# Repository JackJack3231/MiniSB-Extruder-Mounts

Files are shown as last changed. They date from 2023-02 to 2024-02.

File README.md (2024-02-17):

# MiniSB-Extruder-Mounts

Remix of the Mini-Stealthburner to run other Extruders.

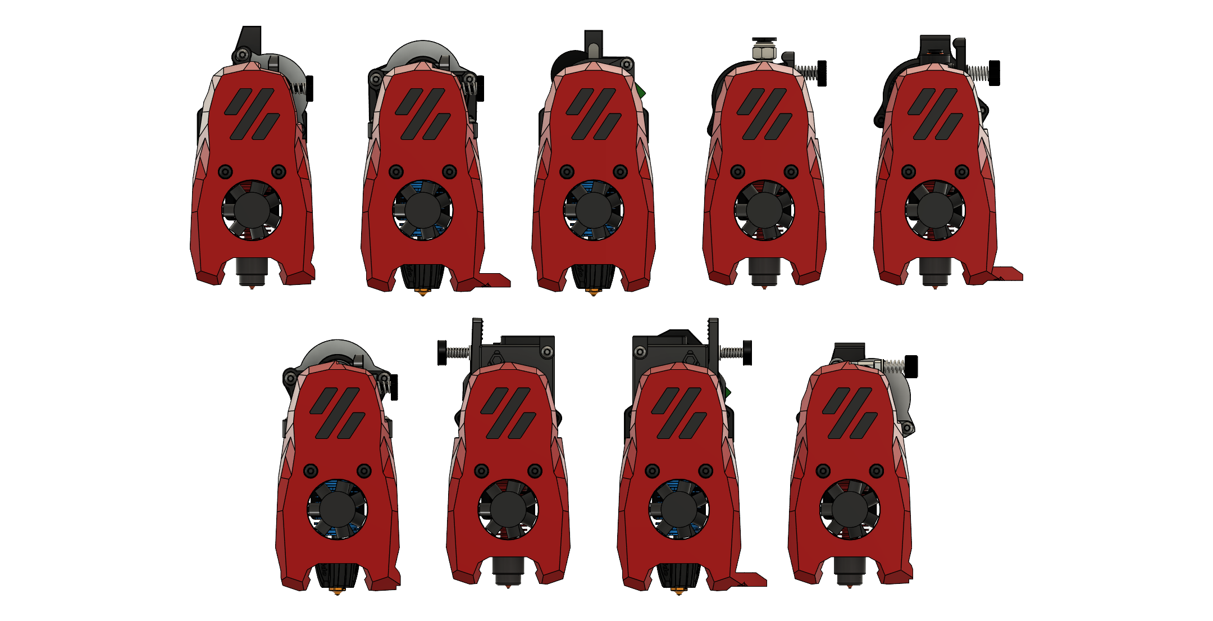
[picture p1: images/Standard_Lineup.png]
Lineup of Standard Extruder-Mounts

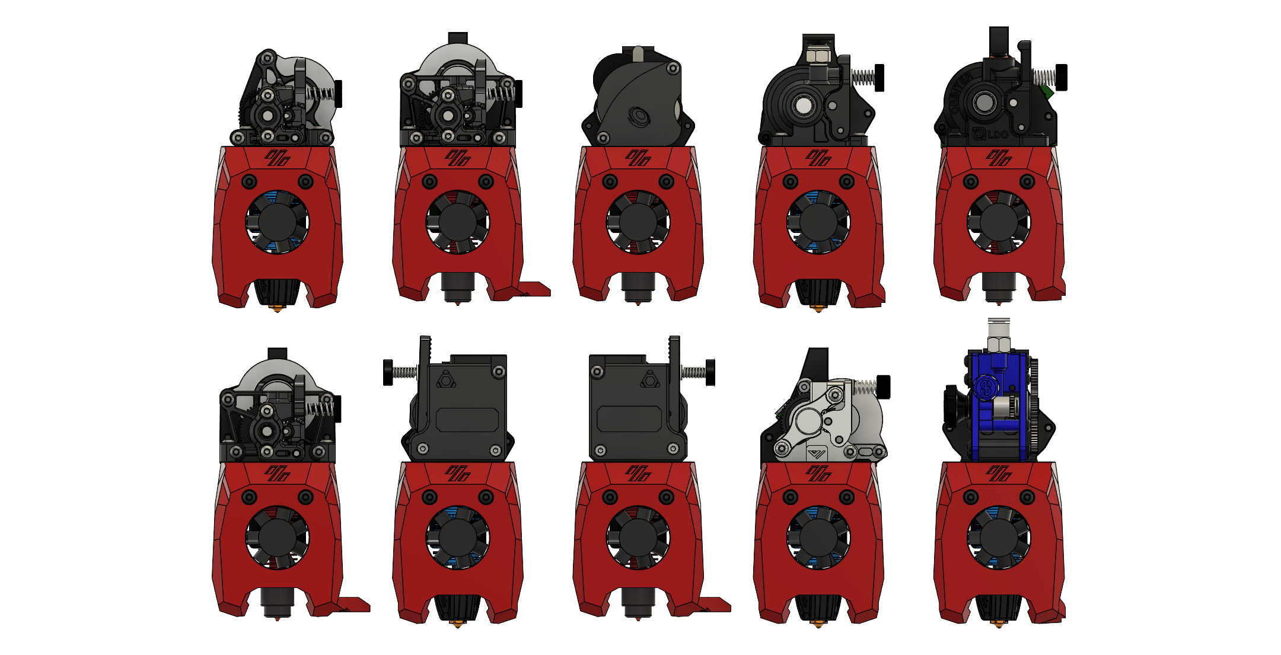
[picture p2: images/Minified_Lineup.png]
Lineup of Minified Extruder-Mounts


This repo includes reworked Files of the Mini-Stealthburner to allow you to use different extruders, namely:

- [Phaetus Apus](https://www.phaetus.com/apus/)
- [Lerdge Aquarius](https://shop.lerdge.com/products/direct-drive-extruder)
- [Haldis HGT](https://www.aliexpress.com/item/1005004816041384.html)
- [Haldis HGX 2.0](https://www.aliexpress.com/item/1005005911670091.html)
- [Haldis HGX-Lite](https://www.aliexpress.com/item/1005004699216563.html)
- [Bondtech LGX-Lite](https://www.bondtech.se/product/lgx-lite-large-gears-extruder/)
- [Mellow Libra Mini](https://www.aliexpress.com/item/1005003506182112.html)
- [Orbiter v1.5](https://orbiterprojects.com/orbiter-1-5/)
- [LDO Orbiter v2.0](https://orbiterprojects.com/orbiter-v2-0/)
- [Annex Engineering Sherpa Heavy](https://github.com/Annex-Engineering/Sherpa_Heavy-Extruder)
- [Annex Engineering Sherpa Micro](https://github.com/Annex-Engineering/Sherpa_Micro-Extruder)
- [Annex Engineering Sherpa Mini](https://github.com/Annex-Engineering/Sherpa_Mini-Extruder)
- TriangleLab TBG-Lite ([Left](https://www.aliexpress.com/item/1005004186141062.html)- and [Right](https://www.aliexpress.com/item/1005003908281100.html)-Version)
- [TriangleLab TBG-S](https://www.aliexpress.com/item/1005005060887127.html)
- [Vz-Hextrudort Low CNC & Vz-Hextrudort Plus CNC](https://github.com/VzBoT3D/Vz-HextrudORT)

The only parts that have changed are the Cowling, Strain-Relief and the Spacers. Everything else is Stock(Hotend Mount, X-Carriage) so this is a drop-in-replacement for Printers with the V0.2-Style X-Carriage.

As I don't have all the extruders some are untested, however if the CAD-Files are accurate they should work fine. This table shows the versions I have verified to work (checkmark):
| Extruder | | Notes |
| --- | --- | ----- |
| Phaetus Apus | :heavy_division_sign: | Assembly works, but needs testing inside a printer |
| Lerdge Aquarius | :heavy_division_sign: | Assembly works, but needs testing inside a printer |
| HGT | :heavy_check_mark: |
| HGX 2.0 | :heavy_check_mark: |
| HGX-Lite | :heavy_division_sign: | Assembly works, but needs testing inside a printer |
| LGX-Lite | :heavy_check_mark: |
| Libra Mini | :grey_question: |
| Orbiter v1.5 | :heavy_division_sign: | Assembly works, but needs testing inside a printer |
| Orbiter v2.0 | :heavy_check_mark: |
| Sherpa Heavy | :grey_question: |
| Sherpa Micro | :heavy_check_mark: |
| Sherpa Mini | :heavy_check_mark: |
| TBG-Lite Left | :heavy_check_mark: |
| TBG-Lite Right | :heavy_check_mark: |
| TBG-S | :heavy_check_mark: |
| Vz-Hextrudort Low CNC | :heavy_check_mark: |
| Vz-Hextrudort Low Plus CNC | :heavy_check_mark: |

## Versions

There are two visual Versions, a "Standard" and a "Minified" Version. The Standard-Version has the upper Logo-Part of the Mini-Stealthburner in front of the Extruder (like [Mavericks LGX-Lite Mod](https://mods.vorondesign.com/detail/nJmiEHmmiI9woW4PqjQ2dA)). The Minified Version doesn't have this cover and is more in line with the Bowden Toolhead or [Mini-AfterSherpa](https://github.com/PrintersForAnts/Mini-AfterSherpa).

### Rapido HF, Dragon UHF and TriangleLab Dragon Ace

Additionally, there are longer cowlings and Hotend mounts to allow you to use a Rapido HF or a Dragon UHF. These versions can be found in the "High_Flow"-Folders of each extruder. **Remember that this will reduce a bit of the usable z height, so update your firmware configuration.**

Also, there is a mount for the [Dragon Ace Hotend](https://www.trianglelab.net/products/dragon-ace%E2%84%A2-hotend) (the mount is exactly the same as the Dragon UHF). With this mount you can use the Dragon Ace with the "Standard Flow" cowlings as it is 3 mm shorter than the Rapido HF or Dragon UHF. Alternatively you can use the spacer that is included with the Dragon ace and use it with the "High Flow" cowlings.

### One Fits Most Version a.k.a. Swiss Cheese

There is a [Version](/Extruder_Mounts/_OneFitsMost/) that aims to support as many extruders as possible, while needing as few printed parts as possible. Dubbed Swiss cheese.

## Bed-Probes

### Boop

The non no probe and ZeroClick cowlings have a cutout for [Boop](https://github.com/PrintersForAnts/Boop).
This is currently untested. The current strain-reliefs and PCB-plates are incompatible,
I recommend using [KayosMakers CANboard Mounts](https://github.com/KayosMaker/CANboard_Mounts).

### Klicky and KlickyNG

For Klicky Users there are cowlings with the probe carrier part for both ["normal" Klicky and KlickyNG](https://github.com/jlas1/Klicky-Probe). The BOM is the same as for a standard Mini-Stealthburner, so for required parts check the [Klicky-Probe GitHub](https://github.com/jlas1/Klicky-Probe).

The Klicky Cowlings have only been test fitted in a V0.2 to check for collisions.
They were not actually used for probing and printing.
As such no docks have been verified to work.

### ZeroClick

Support for the [ZeroClick Probe by zruncho3d](https://github.com/zruncho3d/ZeroClick) is available.

To make space and reduce the chance of collisions, the Dock and Mount have been remade, and special Cowlings are necessary. Also, unlike other remixes of the MiniSB for ZeroClick, this implementation should (barely) allow the use of both Sequin LEDs. More information can be found in the [ZeroClick Common Folder](/Extruder_Mounts/_ZeroClick-Common/).

[Video of ZeroClick in action](https://github.com/JackJack3231/MiniSB-Extruder-Mounts/issues/4#issuecomment-1911860910)

### SuperPINDA, PINDA, M8 inductive probes

SuperPINDA, PINDA and other 8 mm inductive probes are supported. These will require an additional M3x6 BHCS to clamp the probe to the cowling. Clearances are quite tight and there is a very thin wall between the part cooling fan and the probe.

## Strain-Relief and Spacers

Also included are Strain-Reliefs (quickly and crappily thrown together), Mounting Plates for the [Umbilical-PCB by Timmit](https://github.com/VoronDesign/Voron-Hardware/tree/master/V0-Umbilical) and mounting plates for CAN Toolhead boards based on [@KayosMaker/CANboard_Mounts](https://github.com/KayosMaker/CANboard_Mounts). The Umbilical Plates also support the LDO Picobilical. **If you use a PCB Toolhead board please double-check, that the screws on the mounting plate don't short anything!**

The needed Spacers (Size according to CAD) are also included, both in the standard round shape and an octagon version inspired by [KayosMaker](https://github.com/KayosMaker/CANboard_Mounts). The Octagon Spacers are the preferred version, because these don't rely on layer-adhesion for their strength and can be printed lying down instead. Also note that depending on which motor you have on your extruder the Spacer-Length can change because Moons-Motors have a thicker Mounting-Flange (2.5 mm) compared to LDO (2 mm). Keep in mind, when installing the Heatsets into the spacers they can get squished, so the alignment is not 100% correct anymore. If you have issues with this try using longer spacers.

## Print-Instructions

Standard Voron Print-Settings (0.2 mm Layer Height, 4 Perimeters, 40% Infill, 5 Top- and Bottom-Layers). No Supports are needed and all STLs are oriented the correct way and ready to import and print.

## Assembly

Pretty much all the mounts get assembled the same way, important differences get called out in the mount-specific Assembly Manual:

1. Install Heatset-Inserts into Spacers, if your Extruder gets screwed down from the top also install Heatsets into the Cowling
2. Install Fans according to [V0.2 Assembly Manual](https://github.com/VoronDesign/Voron-0/blob/Voron0.2/Manuals/VORON_V0.2_Assembly_Manual.pdf) (page 165-167)
3. Insert the M3 Hex-Nut into the slot on the top of the cowling
4. Secure Extruder to the Cowling with hardware mentioned in the mount-specific BOM
5. Install Hotend, make sure to cut the PTFE-Tube to the correct length.
6. Install everything to the X-Carriage, secure with 2 M3x35 BHCS from the front and 1 M3x20 BHCS from the rear
7. Add Spacers for strain-relief/umbilical plate, you may need to replace some screws to have enough thread to engage with the spacers
8. Add strain-relief/umbilical plate, secure to spacers and X-Carriage

## Credits

The cowling files have been remixed from [Mavericks LGX-Lite Mod](https://mods.vorondesign.com/detail/nJmiEHmmiI9woW4PqjQ2dA).

The Voron [V0.2 files](https://github.com/VoronDesign/Voron-0) have also been used as a reference and are partially included in the CAD-Files uploaded in this repository.

For the umbilical plates [Timmit's PCB CAD](https://github.com/VoronDesign/Voron-Hardware/tree/master/V0-Umbilical) was used.

The CAN-board mounts are remixed from [KayosMakers CANboard Mounts](https://github.com/KayosMaker/CANboard_Mounts)

The Klicky Parts were directly taken from [JosAr's CAD-Files](https://github.com/jlas1/Klicky-Probe) on the Klicky-Probe GitHub.

ZeroClick Parts are based on [zruncho3d's original mod](https://github.com/zruncho3d/ZeroClick).

The CAD-File for the PINDA-Probe was made by Matěj Pavel [Source: GrabCAD](https://grabcad.com/library/prusa-induction-autolevelling-probe-pinda-mk1-1).

Phaetus Hotend CAD-Files come from the [Phaetus GitHub repositories](https://github.com/Phaetus?tab=repositories).

TriangleLab Dragon Ace CAD are from [TriangleLab's Google Drive](https://drive.google.com/drive/folders/11QHxG745J42ZzM7vk0ET1ysG6nBwzrUO).

Sources for the Extruder CAD-Files can be found in the respective README.

## Extras

There are Toolhead Pictures for the Mainsail sidebar included in the Extras Folder.

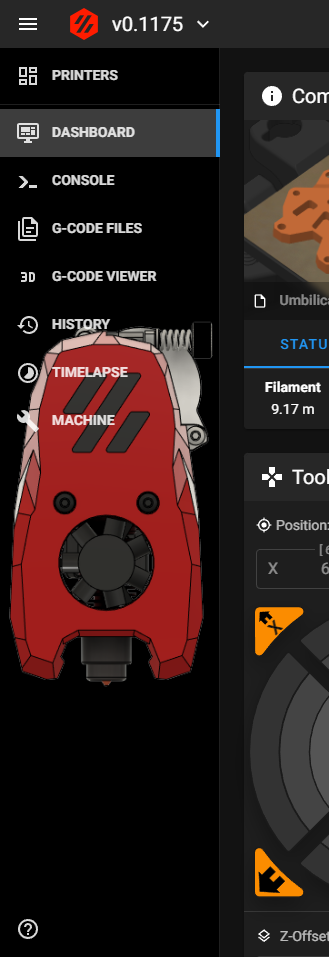
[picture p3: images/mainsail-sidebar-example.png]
Mainsail Sidebar


# Changelog

## 2024-02-17
- Added Support for PINDA and other M8 inductive probes
- Updated Umbilical Plate to support LDO Picobilical
- Move spacers to respective extruder STL-Folders
- Add Labels to cowlings to make them easier to identify
- Updates to Dragon-Ace Hotend Mount
- Fix wrong hole size in Rapido and Dragon UHF Hotend Mount
- Add new Extruders:
    - Haldis HGX Lite
    - Haldis HGX 2.0
    - Haldis HGT
    - Annex Sherpa Heavy
    - TriangleLab TBG-S
    - Lerdge Aquarius
    - Vz-Hextrudort Low Plus CNC

Currently, there are no assembly manuals / documentation for the new extruders

## 2023-12-26

- Added experimental ZeroClick support. Progresses [#4](https://github.com/JackJack3231/MiniSB-Extruder-Mounts/issues/4)
- Added Dragon Ace Mount
- Spelling and grammar fixes in the repo

## 2023-11-15

- Added experimental Boop Support
- Fixed STL names of OneFitsMost, Sherpa Micro and TBG-Lite Left
- (Re-) Added a small gap to the hexagonal contact between x-carriage and cowling, like in the original Mini-Stealthburner

## 2023-08-29 Late August Update

- Remade all the CAD-Files. This was mainly to make updating in the future easier and faster. This resulted in cosmetic changes to all the cowlings and the umbilical plates. Strain relief plates have been altered in their height to be more consistent, the old STLs are still available in the Legacy folders.
- Changed naming scheme of most STLs to make files easier to identify
- Promoted HF-Cowlings from experimental to full release.
- Updated Dragon UHF and Rapido Mount to use Holes for M2.5 instead of M3 screws.
- Added Klicky and KlickyNG Cowlings (untested).
- Added CAN-Board mounts (untested).
- Orbiter v2.0: Dropped the "Offset"-Versions for now, unless someone wants them back.
- Apus: Removed the "printed Adapter"-Cowling, as there is now enough space for the Heatsets with the default adapter in the cowling because the Hex-nut was moved back a bit in the last update. There still is a printable adapter for people that don't have the default adapter anymore.

## 2023-08-17

- Added LGX-Lite Mounts. As Maverick hasn't updated the original Mod to the R1 ducts, I decided to add updated LGX-Lite Mounts to this repo. This includes Strain Relief, Umbilical Plate and a Minified Version.
- Added small hexagonal shape to the rear of the cowling. This makes it slot into the X-Carriage even more, thanks [@probably-Erwins-Cat](https://github.com/probably-Erwins-Cat) for pointing that out. Closes [#3](https://github.com/JackJack3231/MiniSB-Extruder-Mounts/issues/3)
- Moved Hex nut in the cowling back 2 mm so now a M3x20 BHCS can be used to secure the cowling from the back instead of a M3x22.

## 2023-07-29:

- Update Rapido Cowlings to use R1-style part-cooling-ducts (a bit ugly but should work pretty well)
- Add Dragon UHF Mount, as it should work just like the Rapido HF
- Update One Fits Most Version to use R1 part-cooling-ducts (missed that last time)

## 2023-06-13:

- Update Cowling ducts to the improved ones from the [V0.2r1 Release](https://github.com/VoronDesign/Voron-0#v02r1-2023-june). Rapido Cowlings are using the old ducts for now.

## 2023-06-06:

- Add Experimental Rapido HF Cowlings based on [Mavericks mod](https://mods.vorondesign.com/detail/dWZjGJ83RbTpRTdYYRwng).

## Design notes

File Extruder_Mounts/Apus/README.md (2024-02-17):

# MiniSB Apus Extruder - Untested

Because of the unique Shape of the Apus-Extruder there is only a Minified Version.

This Mount has not been tested in an actual printer, however outside everything fits fine. So double check that your wiring doesn't hit anything in the back of the printer.

## BOM

| Part | Quantity | Notes |
| --- | --- | --- |
| M3x5x4 Heatset | 8 | |
| M3x4.2x3 Heatset | 2 | Only needed when using printed Apus Adapter piece |
| M3x35 BHCS | 2 | |
| M3x20 BHCS | 1 | |
| M3x12 BHCS | 4 | Should be included with the Apus Extruder |
| M3x6 BHCS | 4 |
| M3 Hex nut | 1 |
| 3010 Axial Fan | 1 |
| 3010 Blower Fan | 2 |
| Hotend | 1 | There are a number of supported Hotends, check the V0.2 GitHub for options |
| Apus Extruder | 1 |
| | | |
| **Additional Parts for standard strain relief** |
| M3x8 BHCS | 2 | |
| **Additional Parts for Umbilical PCB** |
| M3x8 BHCS | 2 | |
| M3x6 BHCS | 2 | |
| **Additional Parts for CAN Toolheads** |
| M3x6 BHCS | 4 | |

## Images

### Minified

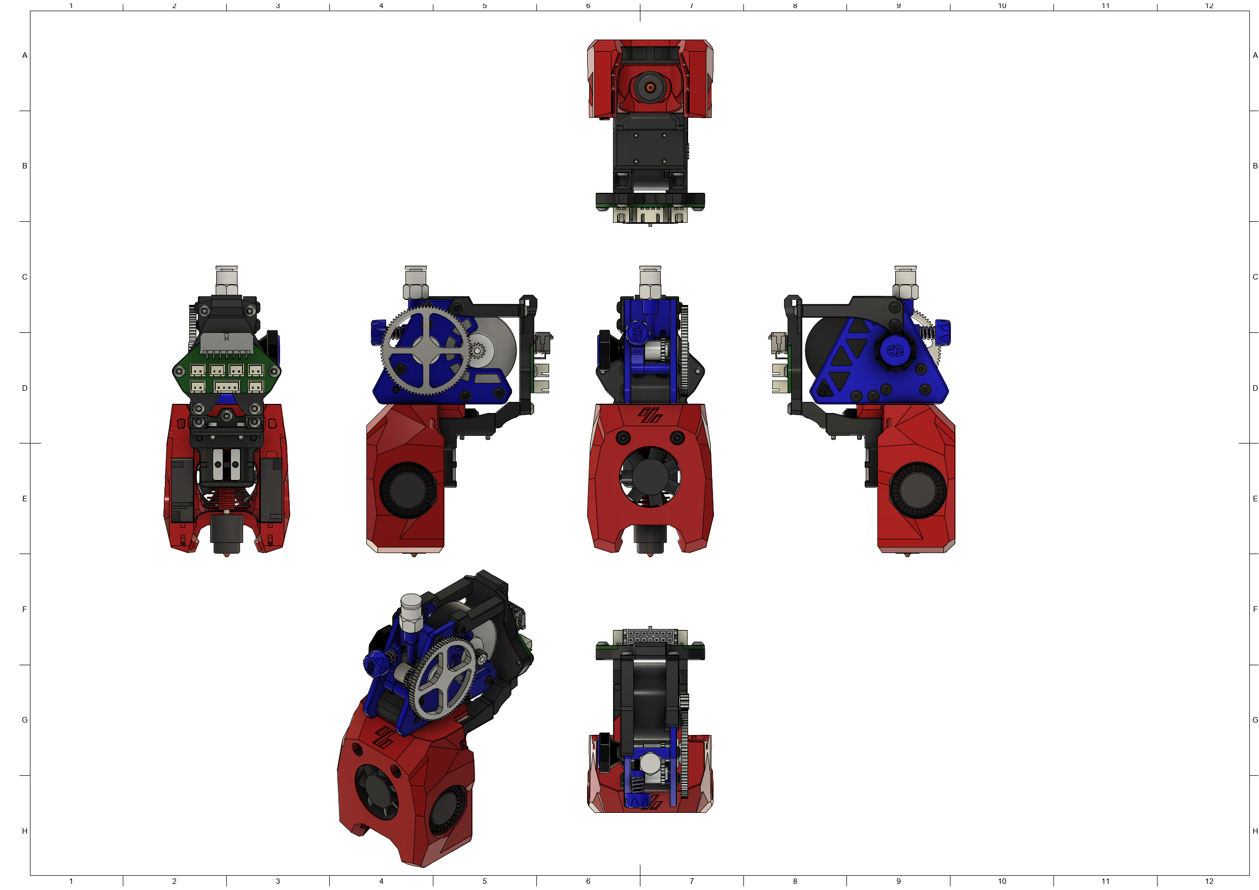
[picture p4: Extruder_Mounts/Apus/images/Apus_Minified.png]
Minified


## CAD-Source

The source for the CAD-File of the extruder is the [Phaetus Apus GitHub repository](https://github.com/Phaetus/Apus)

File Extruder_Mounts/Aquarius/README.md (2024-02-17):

# MiniSB Lerdge Aquarius

## About the Stock Motor

It seems like at some point the stock motor that can be bought with this Extruder changed.
In the CAD and on most product pages the motor is 25.5 mm long. However, some units are only 22 mm long.
If you received one of the shorter motors you might be able to use the MOONS spacers and no bottom spacers for the strain relief. If you have the longer motor you will need the bottom spacer and `Stock_Motor` Spacers.

## BOM

| Part | Quantity | Notes |
| --- | --- | --- |
| M3x5x4 Heatset Insert | 4 |
| M3x35 BHCS | 2 | |
| M3x20 BHCS | 1 |
| M3x6 BHCS | 2 |
| M3x8 FHCS | 2 | Should be included with the extruder |
| M3 Hex nut | 1 |
| 3010 Axial Fan | 1 |
| 3010 Blower Fan | 2 |
| Hotend | 1 | There are a number of supported Hotends, check the V0.2 GitHub for options |
| Lerdge Aquarius Extruder | 1 |
| | | |
| **Additional Parts required when using the stock motor (> 21 mm length)** |
| M3x12 BHCS | 2 |
| **Additional Parts for standard strain relief** |
| M3x8 BHCS | 2 | Only for shorter motors |
| **Additional Parts for Umbilical PCB** |
| M3x8 BHCS | 2 | Only for shorter motors |
| M3x6 BHCS | 2 | |
| **Additional Parts for CAN Toolheads** |
| M3x6 BHCS | 2 |
| M3x6 BHCS | 2 | Only for shorter motors |

## Printed Parts

- 1x Hotend Mount
- 1x Cowling of your choice
- 1x Strain Relief Plate for your wiring setup (CAN, Timmit Umbilical or stock)
- 2x Spacer Octagon or Round according to your used motor
- 1x PTFE-Guide

If you are using a motor which is longer than 21 mm, like the stock motor sold as an option with this extruder, you will need to print the plates and spacers marked `Stock_Motor`.

## Images

### Standard

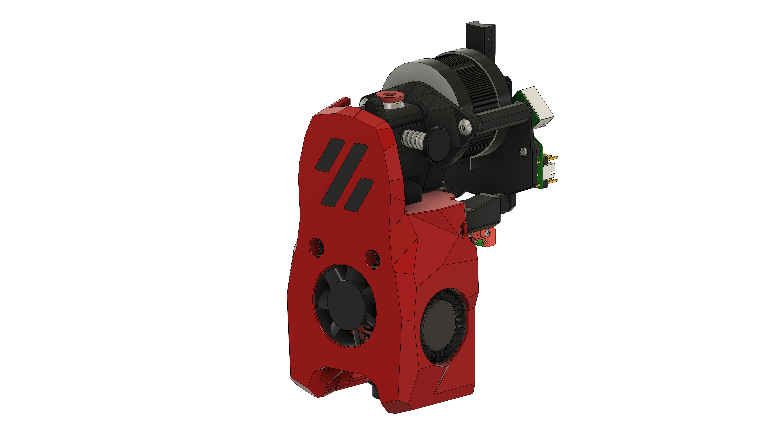
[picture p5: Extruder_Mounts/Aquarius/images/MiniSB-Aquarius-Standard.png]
Standard


### Minified

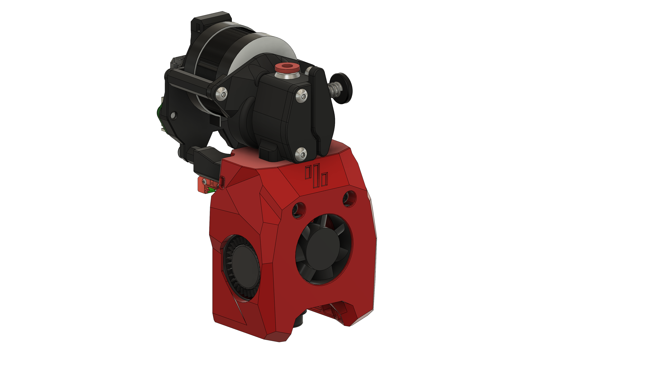
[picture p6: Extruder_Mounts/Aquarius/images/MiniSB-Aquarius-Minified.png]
Minified


## CAD-Source

The CAD-File of the extruder was provided by Lerdge upon request.

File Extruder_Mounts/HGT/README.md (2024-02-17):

# MiniSB HGT

## BOM

| Part | Quantity | Notes |
| --- | --- | --- |
| M3x5x4 Heatset Insert | 2 |
| M3x35 BHCS | 2 | |
| M3x20 BHCS | 1 | |
| M3x8 SHCS | 2 | Should be included with the HGT-Extruder Extruder |
| M3x6 BHCS | 1 |
| M3x12 FHCS | 1 
| M3 Hex nut | 1 |
| 3010 Axial Fan | 1 |
| 3010 Blower Fan | 2 |
| Hotend | 1 | There are a number of supported Hotends, check the V0.2 GitHub for options |
| HGT Extruder | 1 |
| | | |
| **Additional Parts for standard strain relief** |
| M3x8 BHCS | 2 | |
| **Additional Parts for Umbilical PCB** |
| M3x8 BHCS | 2 | |
| M3x6 BHCS | 2 | |
| **Additional Parts for CAN Toolheads** |
| M3x6 BHCS | 4 | |

## Images

### Standard

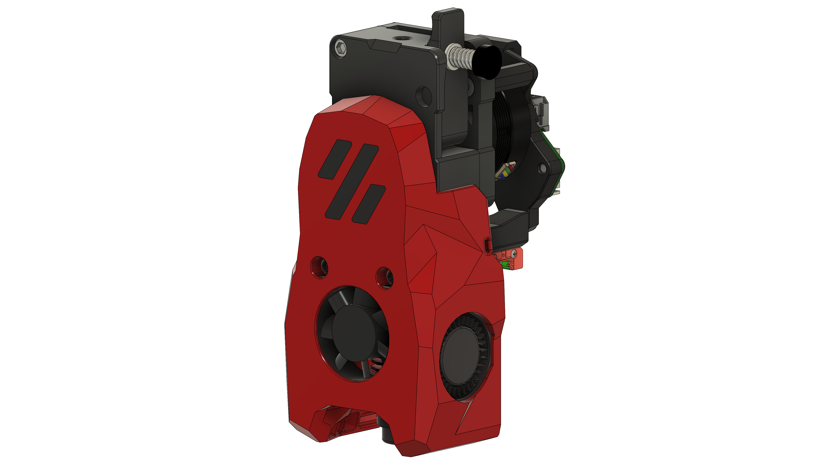
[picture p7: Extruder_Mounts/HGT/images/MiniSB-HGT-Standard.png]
Standard


### Minified

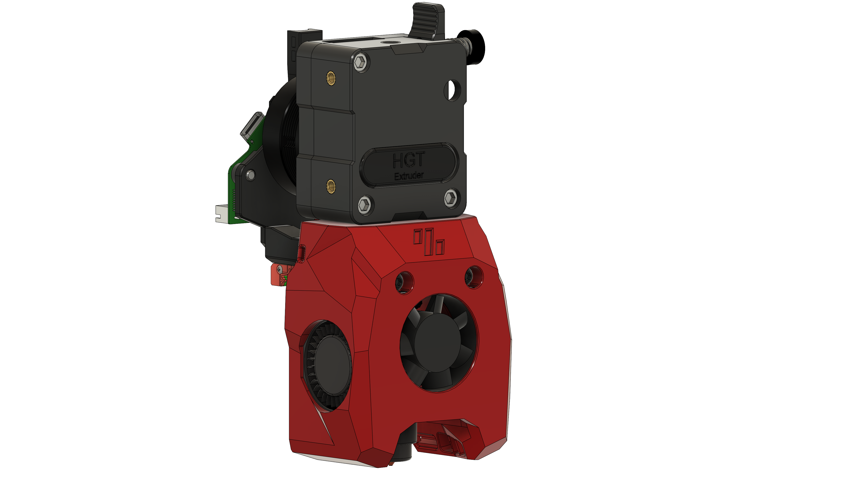
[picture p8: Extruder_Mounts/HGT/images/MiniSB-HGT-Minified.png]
Minified


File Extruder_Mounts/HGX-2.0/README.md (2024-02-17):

# MiniSB HGX 2.0

## BOM

| Part | Quantity | Notes |
| --- | --- | --- |
| M3x5x4 Heatset Insert | 2 |
| M3x35 BHCS | 2 | |
| M3x20 BHCS | 1 | |
| M3x8 SHCS | 3 | Should be included with the HGX 2.0 Extruder |
| M3x6 BHCS | 1 |
| M3x8 FHCS | 1 
| M3 Hex nut | 1 |
| 3010 Axial Fan | 1 |
| 3010 Blower Fan | 2 |
| Hotend | 1 | There are a number of supported Hotends, check the V0.2 GitHub for options |
| HGX 2.0 Extruder | 1 |
| | | |
| **Additional Parts for standard strain relief** |
| M3x8 BHCS | 2 | |
| **Additional Parts for Umbilical PCB** |
| M3x8 BHCS | 2 | |
| M3x6 BHCS | 2 | |
| **Additional Parts for CAN Toolheads** |
| M3x6 BHCS | 4 | |

## Images

### Standard

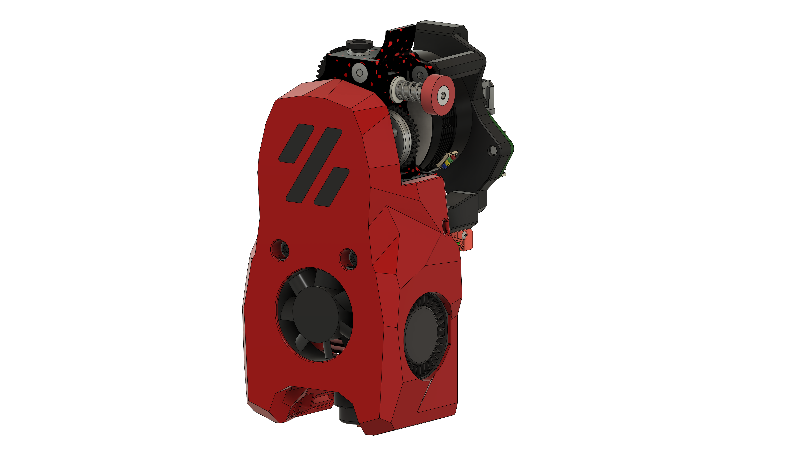
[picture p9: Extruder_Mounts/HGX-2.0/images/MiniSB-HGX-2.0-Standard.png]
Standard


### Minified

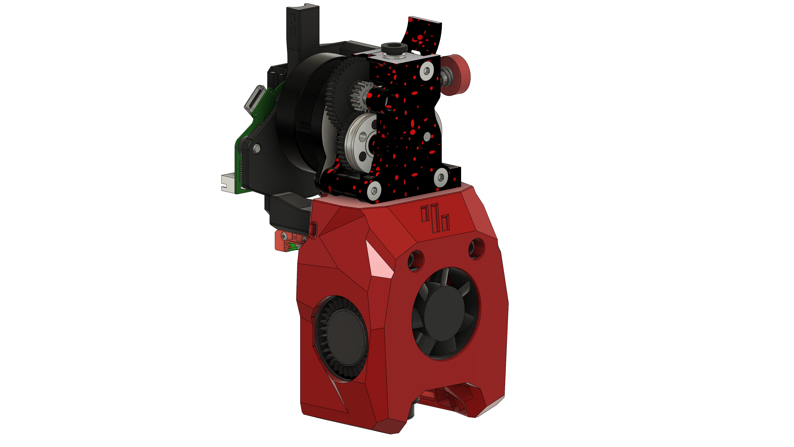
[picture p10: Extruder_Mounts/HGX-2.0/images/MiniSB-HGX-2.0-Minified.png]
Minified


## CAD-Source

The Extruder CAD-Model was created by me (JackJack3231).

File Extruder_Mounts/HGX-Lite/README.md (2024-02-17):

# MiniSB HGX Lite

## BOM

| Part | Quantity | Notes |
| --- | --- | --- |
| M3x5x4 Heatset Insert | 6 |
| M3x35 BHCS | 2 | |
| M3x20 BHCS | 1 | |
| M3x12 BHCS | 2 | Should be included with the HGX Lite Extruder |
| M3x6 BHCS | 2 |
| M3 Hex nut | 1 |
| 3010 Axial Fan | 1 |
| 3010 Blower Fan | 2 |
| Hotend | 1 | There are a number of supported Hotends, check the V0.2 GitHub for options |
| HGX Lite Extruder | 1 |
| | | |
| **Additional Parts when using the Stock Motor** |
| M3x5x4 Heatset Insert | 2 |
| **Additional Parts for standard strain relief** |
| M3x8 BHCS | 2 | |
| M3x6 BHCS | 2 | For Stock Motor |
| **Additional Parts for Umbilical PCB** |
| M3x8 BHCS | 2 | |
| M3x6 BHCS | 2 | For shorter motors |
| M3x10 BHCS | 2 | For stock motor |
| **Additional Parts for CAN Toolheads** |
| M3x6 BHCS | 2 | |
| M3x6 BHCS | 2 | For shorter motors |
| M3x10 BHCS | 2 | For stock motor |

## Images

### Standard

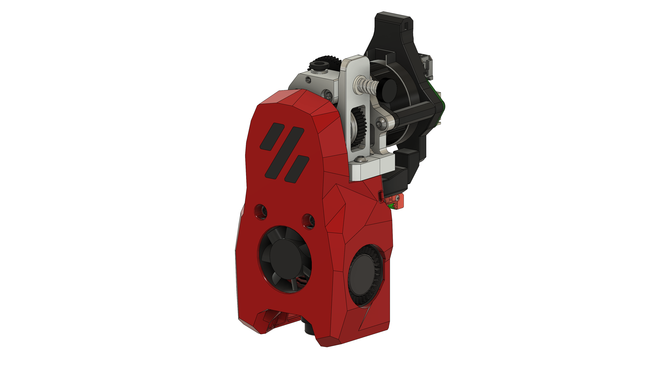
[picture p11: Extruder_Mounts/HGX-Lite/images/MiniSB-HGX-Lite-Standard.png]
Standard


### Minified

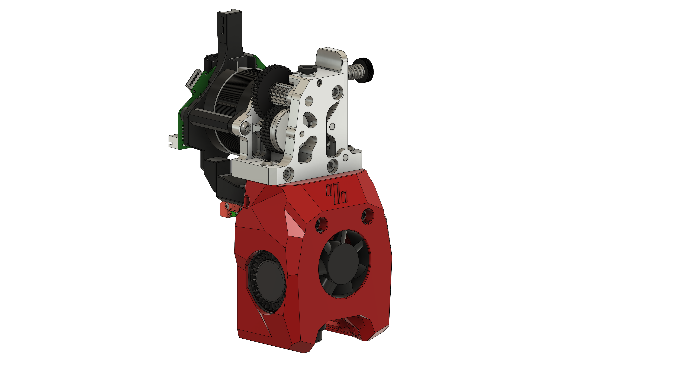
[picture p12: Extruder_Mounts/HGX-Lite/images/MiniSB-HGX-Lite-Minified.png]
Minified


## CAD-Source

The Extruder CAD-Model is based on the [HGX LITE to SV06 mod by Gumo Design](https://www.printables.com/en/model/556167-hgx-lite-to-sv06-mod/files)

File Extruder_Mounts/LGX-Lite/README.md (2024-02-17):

# MiniSB LGX Lite

## BOM

| Part | Quantity | Notes |
| --- | --- | --- |
| M3x5x4 Heatset Insert | 4 |
| M3x35 BHCS | 2 | |
| M3x30 BHCS | 2 | Optional to replace Motor Screws |
| M3x20 BHCS | 1 | |
| M3x8 BHCS | 4 |
| M3x6 BHCS | 2 |
| M3 Hex nut | 1 |
| 3010 Axial Fan | 1 |
| 3010 Blower Fan | 2 |
| Hotend | 1 | There are a number of supported Hotends, check the V0.2 GitHub for options |
| Bondtech LGX-Lite Extruder | 1 |
| | | |
| **Additional Parts for standard strain relief** |
| M3x8 BHCS | 2 |
| **Additional Parts for Umbilical PCB** |
| M3x8 BHCS | 2 |
| M3x6 BHCS | 2 | |
| **Additional Parts for CAN Toolheads** |
| M3x6 BHCS | 4 | |

## Images

### Standard

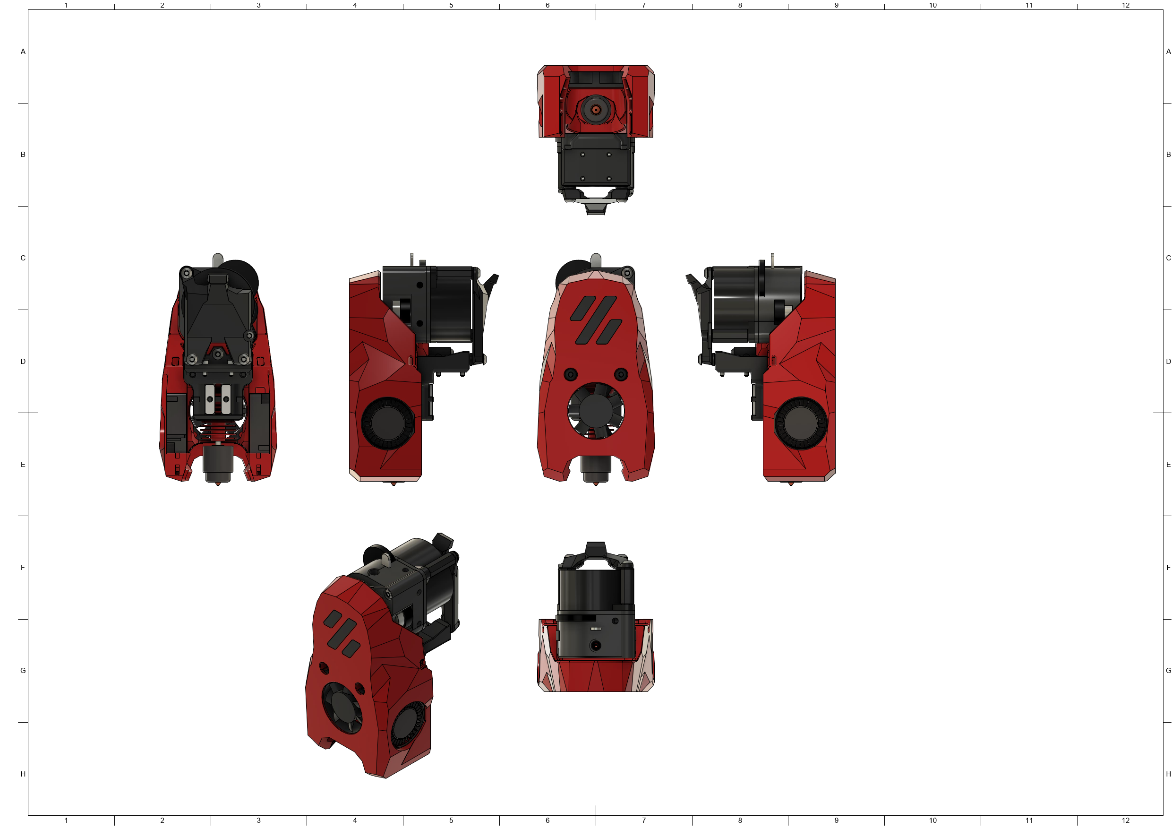
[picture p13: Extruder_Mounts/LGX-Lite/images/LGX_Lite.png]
Standard


### Minified

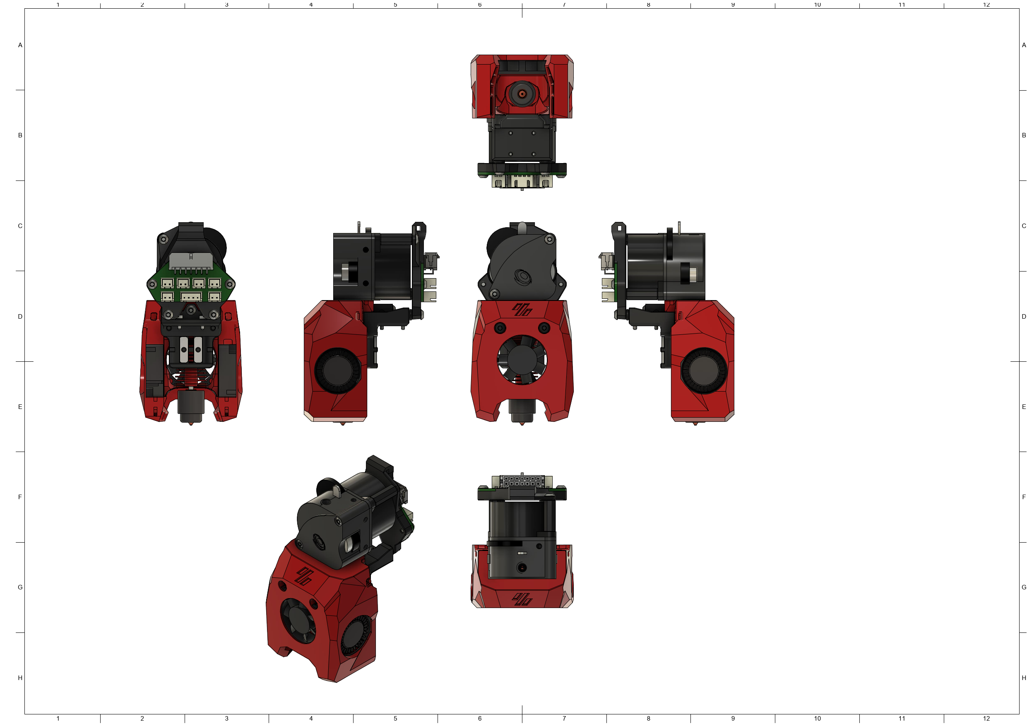
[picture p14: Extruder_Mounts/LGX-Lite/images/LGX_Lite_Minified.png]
Minified


## CAD-Source

The source for the CAD-File of the extruder is [Mavericks LGX-Lite Mod](https://mods.vorondesign.com/detail/nJmiEHmmiI9woW4PqjQ2dA)

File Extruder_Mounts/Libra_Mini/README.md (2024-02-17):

# MiniSB Libra Mini (Untested)

## BOM

| Part | Quantity | Notes |
| --- | --- | --- |
| M3x5x4 Heatset Insert | 6 | |
| M3x35 BHCS | 2 | |
| M3x20 BHCS | 1 |
| M3x16 BHCS | 2 |
| M3x12 BHCS | 2 | |
| M3x6 BHCS | 2 | |
| M3 Hex nut | 1 |
| 3010 Axial Fan | 1 |
| 3010 Blower Fan | 2 |
| Hotend | 1 | There are a number of supported Hotends, check the V0.2 GitHub for options |
| Libra Mini Extruder | 1 |
| | | |
| **Additional Parts for standard strain relief** |
| M3x8 BHCS | 2 |
| **Additional Parts for Umbilical PCB** |
| M3x8 BHCS | 2 |
| M3x6 BHCS | 2 | |
| **Additional Parts for CAN Toolheads** |
| M3x6 BHCS | 4 | |

## Images

### Standard

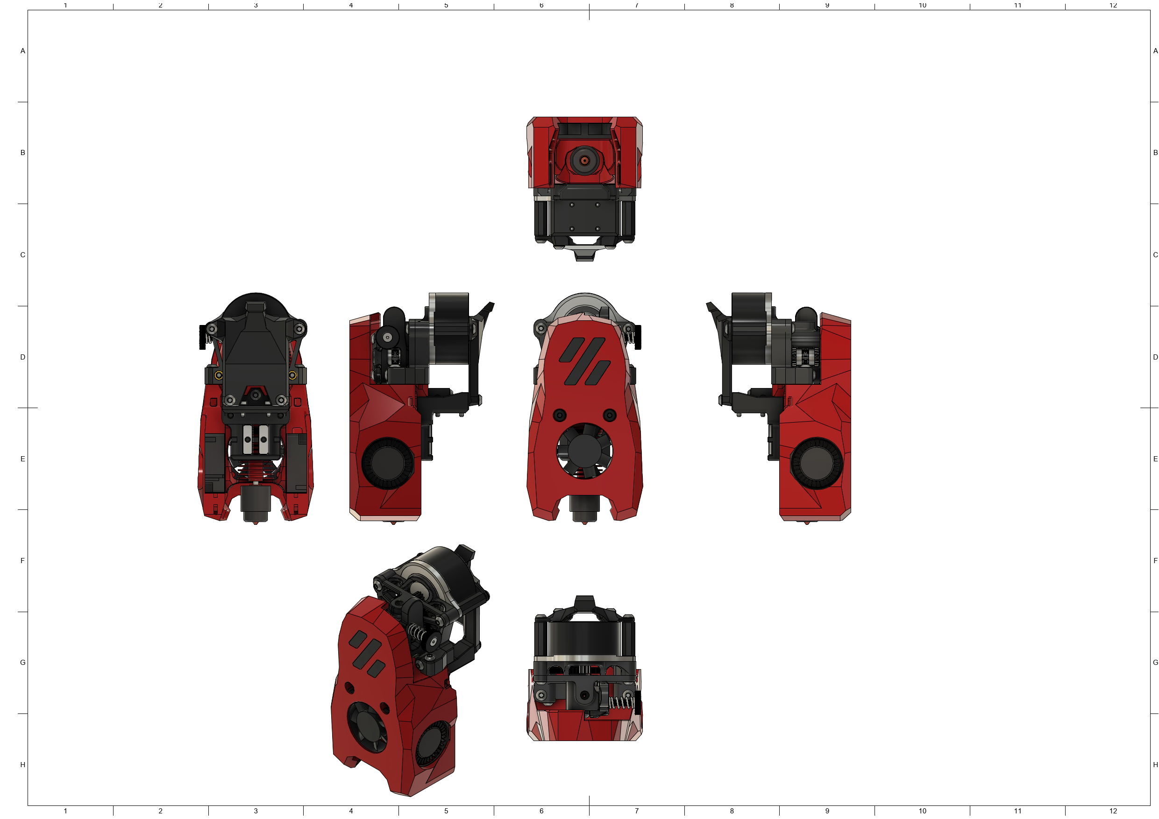
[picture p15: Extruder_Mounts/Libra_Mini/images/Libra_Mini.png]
Standard


### Minified

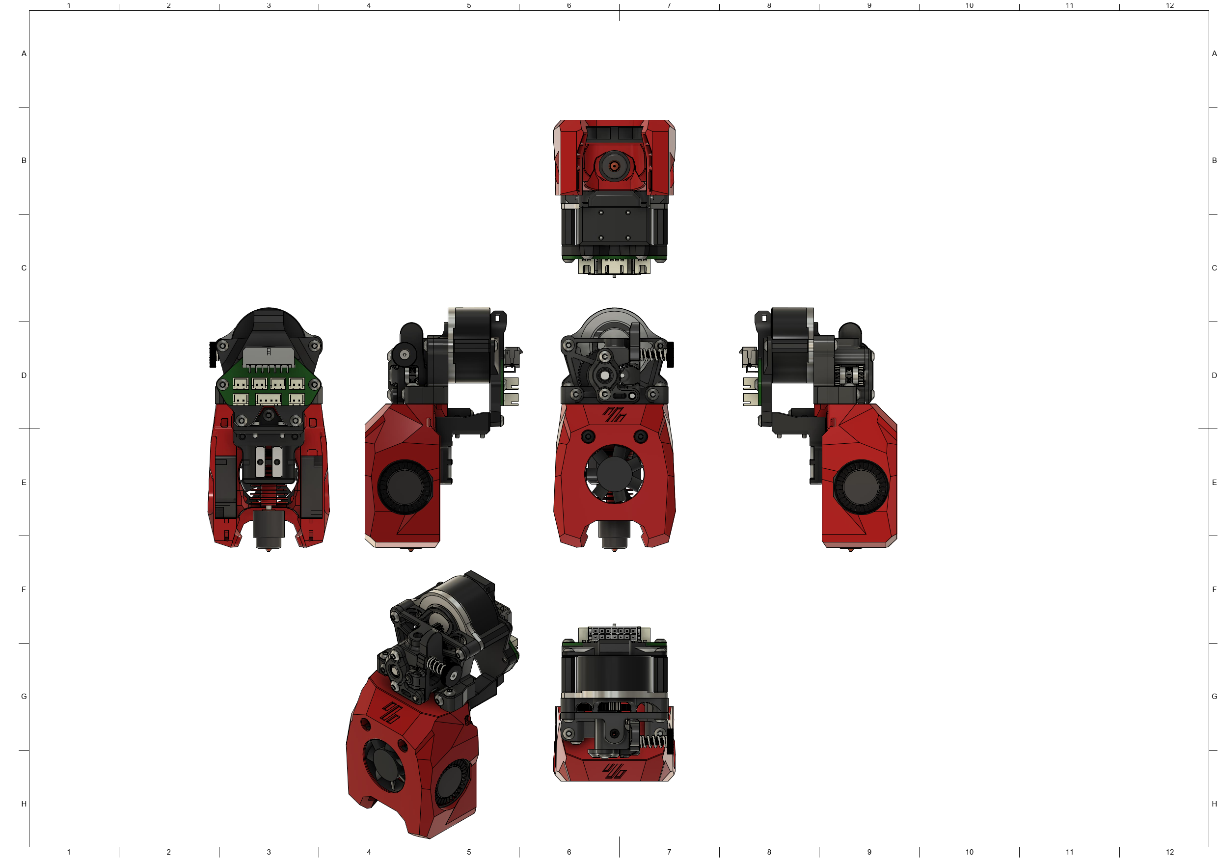
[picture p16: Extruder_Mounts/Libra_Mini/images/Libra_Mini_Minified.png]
Minified


## CAD-Source

The source for the CAD-File of the extruder is the [Mellow Libra Mini GitHub repository](https://github.com/Mellow-3D/Libra-Mini)

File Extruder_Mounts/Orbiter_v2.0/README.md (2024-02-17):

# MiniSB Orbiter v2.0

## BOM

| Part | Quantity | Notes |
| --- | --- | --- |
| M3x5x4 Heatset Insert | 6 | |
| M3x35 BHCS | 2 | |
| M3x20 BHCS | 1 | |
| M3x8 BHCS | 2 |
| M3x6 BHCS | 2 |
| M3 Hex nut | 1 |
| 3010 Axial Fan | 1 |
| 3010 Blower Fan | 2 |
| Hotend | 1 | There are a number of supported Hotends, check the V0.2 GitHub for options |
| Orbiter v2.0 Extruder | 1 |
| | | |
| **Additional Parts for standard strain relief** |
| M3x8 BHCS | 2 | |
| **Additional Parts for Umbilical PCB** |
| M3x8 BHCS | 2 | |
| M3x6 BHCS | 2 | |
| **Additional Parts for CAN Toolheads** |
| M3x6 BHCS | 4 | |

## Images

### Standard

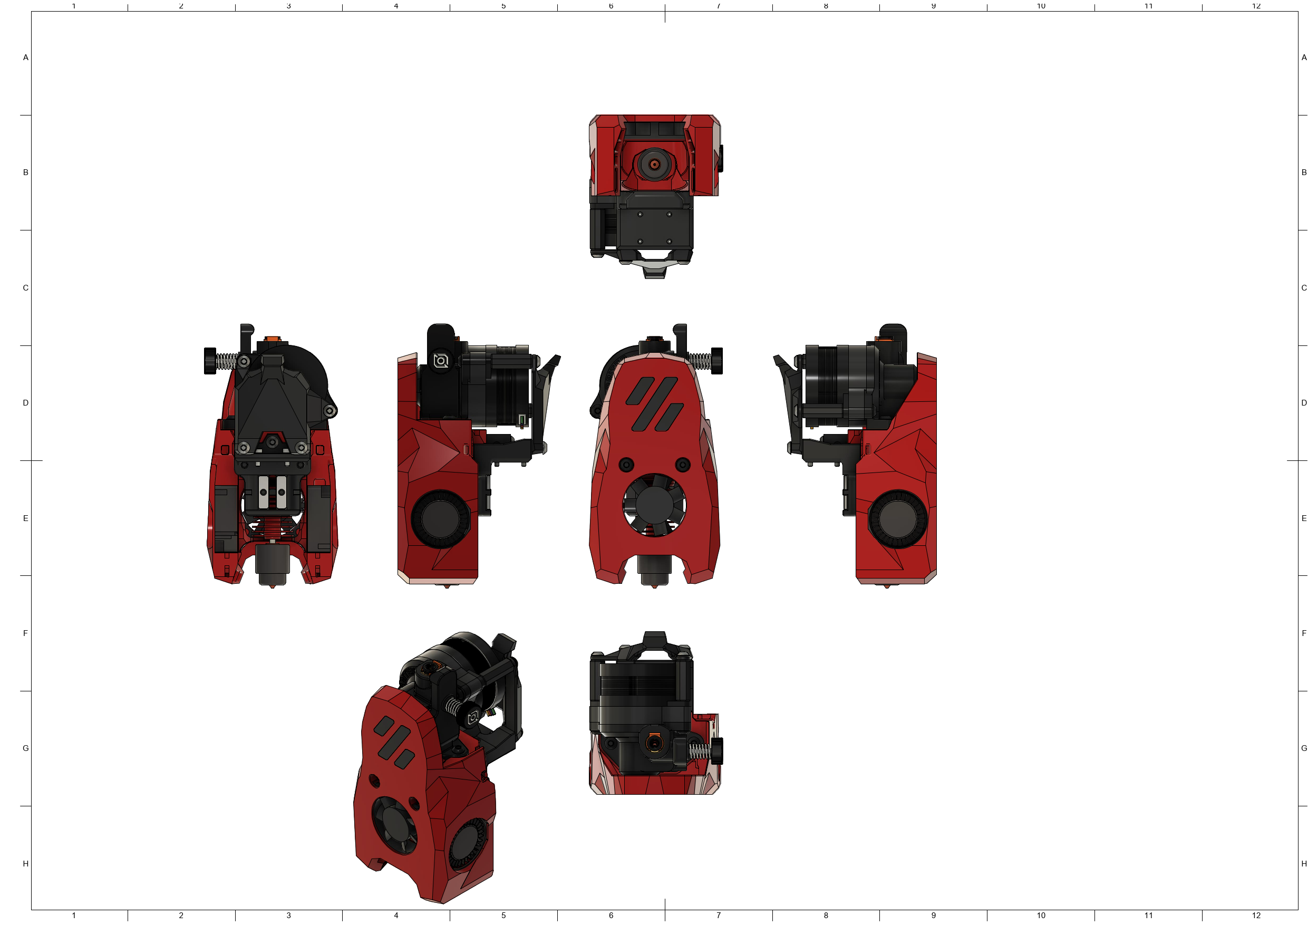
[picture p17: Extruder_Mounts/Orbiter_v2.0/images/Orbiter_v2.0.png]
Standard


### Minified

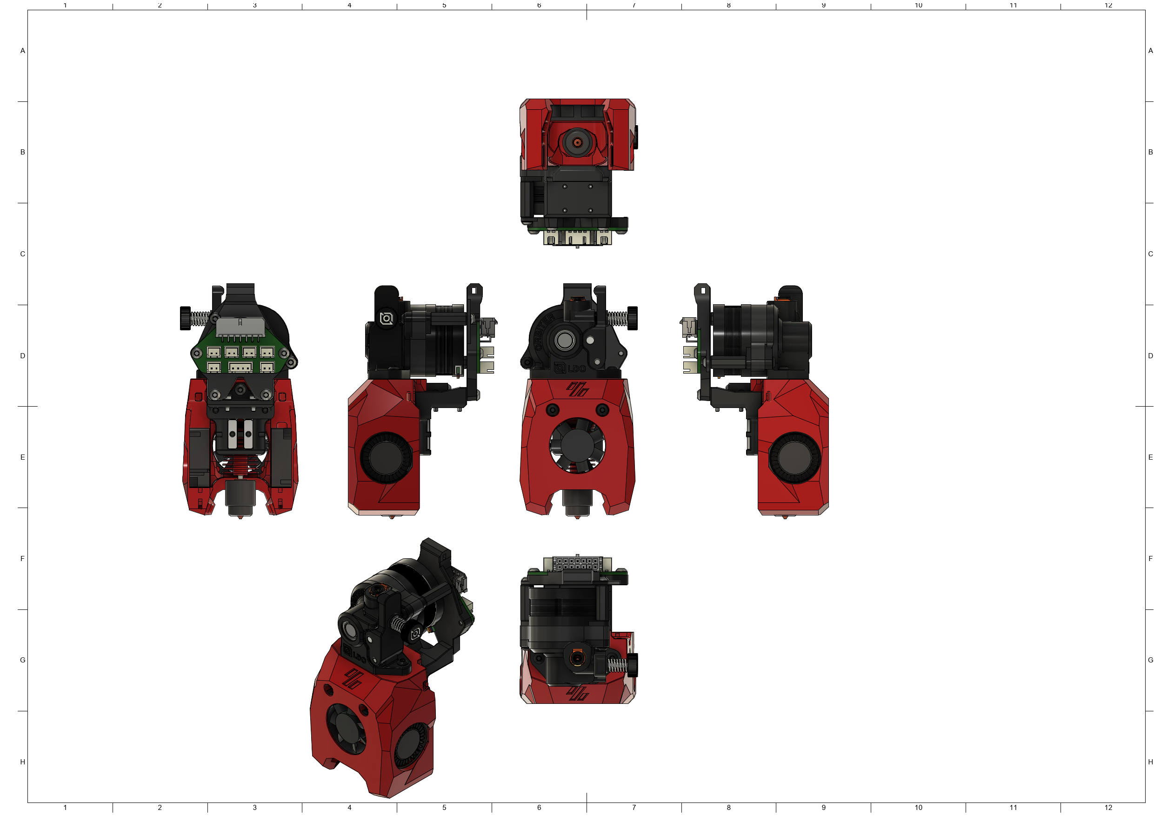
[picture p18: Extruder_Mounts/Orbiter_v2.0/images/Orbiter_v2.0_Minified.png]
Minified


## CAD-Source

The source for the CAD-File of the extruder is the [Orbiter v2.0 project page](https://www.orbiterprojects.com/orbiter-v2-0/)

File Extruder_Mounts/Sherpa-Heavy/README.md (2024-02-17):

# MiniSB Sherpa Heavy

## BOM

| Part | Quantity | Notes |
| --- | --- | --- |
| M3x5x4 Heatset Insert | 2 |
| M3x35 BHCS | 2 | |
| M3x20 BHCS | 1 | |
| M3x18 BHCS | 2 |
| M3x12 BHCS | 2 | |
| M3 Hex nut | 1 |
| 3010 Axial Fan | 1 |
| 3010 Blower Fan | 2 |
| Hotend | 1 | There are a number of supported Hotends, check the V0.2 GitHub for options |
| Sherpa Heavy Extruder | 1 |
| | | |
| **Additional Parts for standard strain relief** |
| M3x8 BHCS | 2 | |
| **Additional Parts for Umbilical PCB** |
| M3x8 BHCS | 2 | |
| M3x6 BHCS | 2 | |
| **Additional Parts for CAN Toolheads** |
| M3x6 BHCS | 4 | |

## Images

### Standard

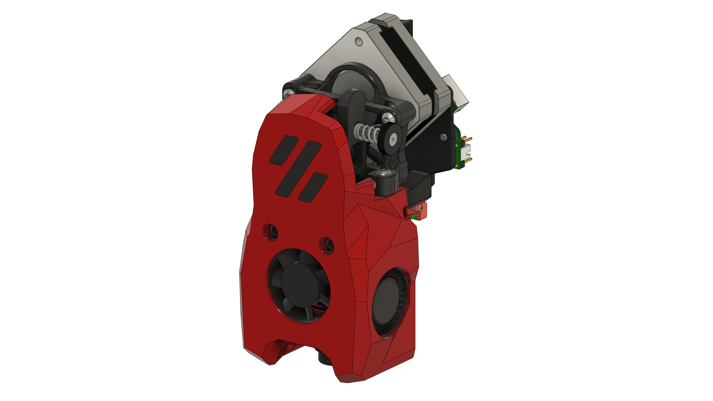
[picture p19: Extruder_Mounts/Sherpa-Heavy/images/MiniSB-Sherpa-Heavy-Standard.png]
Standard


### Minified

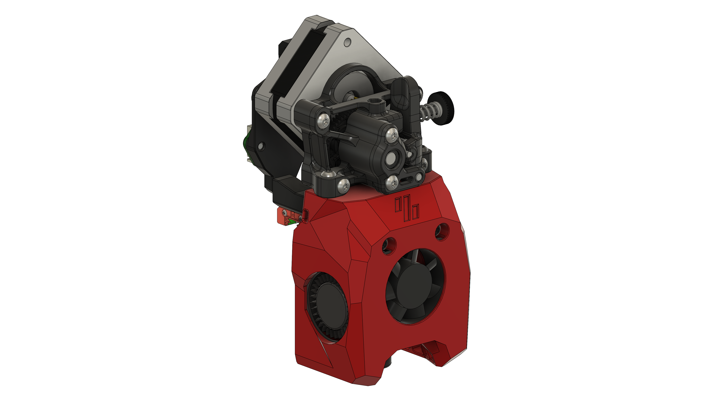
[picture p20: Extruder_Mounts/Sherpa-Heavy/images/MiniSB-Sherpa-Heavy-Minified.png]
Minified


## CAD-Source

The source for the CAD-File of the extruder is the [Sherpa Heavy GitHub repository](https://github.com/Annex-Engineering/Sherpa_Heavy-Extruder)

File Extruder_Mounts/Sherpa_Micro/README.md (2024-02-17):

# MiniSB Sherpa Micro

## BOM

| Part | Quantity | Notes |
| --- | --- | --- |
| M3x5x4 Heatset Insert | 6 |
| M3x35 BHCS | 2 | |
| M3x25 BHCS | 1 | |
| M3x20 BHCS | 1 | |
| M3x16 BHCS | 1 |
| M3x12 BHCS | 2 |
| M3x6 BHCS | 2 |
| M3 Hex nut | 1 |
| 3010 Axial Fan | 1 |
| 3010 Blower Fan | 2 |
| Hotend | 1 | There are a number of supported Hotends, check the V0.2 GitHub for options |
| Sherpa Micro Extruder | 1 |
| | | |
| **Additional Parts for standard strain relief** |
| M3x8 BHCS | 2 | |
| **Additional Parts for Umbilical PCB** |
| M3x8 BHCS | 2 | |
| M3x6 BHCS | 2 | |
| **Additional Parts for CAN Toolheads** |
| M3x6 BHCS | 4 | |

## Images

### Standard

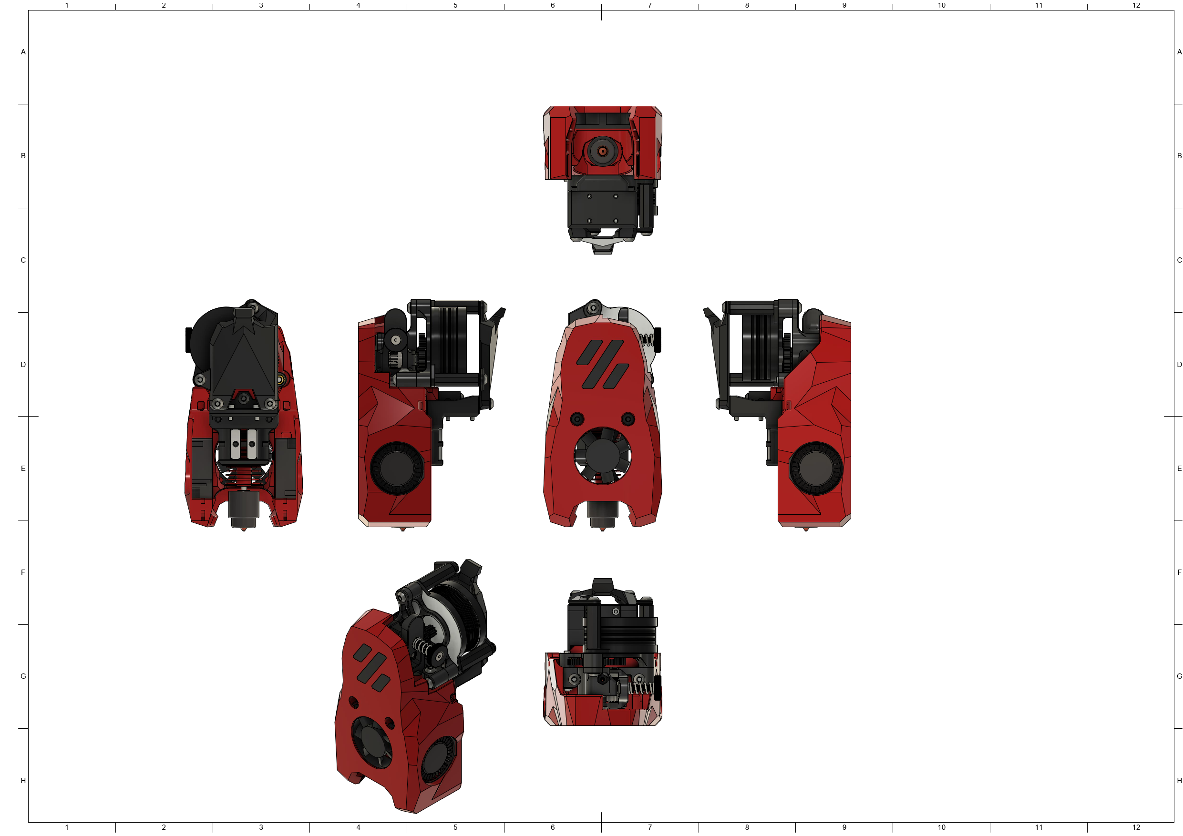
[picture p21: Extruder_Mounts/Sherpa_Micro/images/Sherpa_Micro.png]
Standard


### Minified

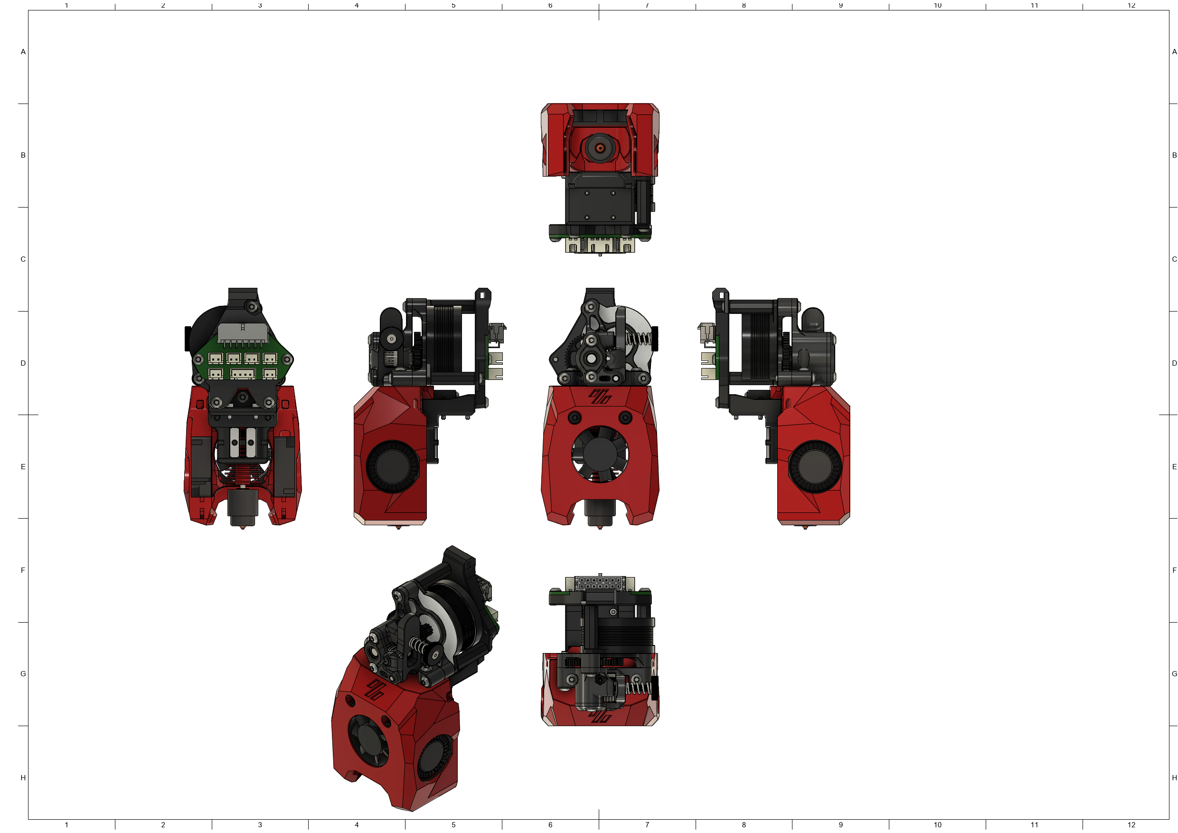
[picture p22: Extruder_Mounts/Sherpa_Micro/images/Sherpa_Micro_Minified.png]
Minified


## CAD-Source

The source for the CAD-File of the extruder is the [Sherpa Micro GitHub repository](https://github.com/Annex-Engineering/Sherpa_Micro-Extruder)

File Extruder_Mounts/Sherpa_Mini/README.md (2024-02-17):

# MiniSB Sherpa Mini

## BOM

| Part | Quantity | Notes |
| --- | --- | --- |
| M3x5x4 Heatset Insert | 6 |
| M3x35 BHCS | 2 | |
| M3x20 BHCS | 1 | |
| M3x16 BHCS | 2 | |
| M3x6 BHCS | 2 | |
| M3 Hex nut | 1 |
| 3010 Axial Fan | 1 |
| 3010 Blower Fan | 2 |
| Hotend | 1 | There are a number of supported Hotends, check the V0.2 GitHub for options |
| Sherpa Mini Extruder | 1 |
| | | |
| **Additional Parts for standard strain relief** |
| M3x8 BHCS | 2 | |
| **Additional Parts for Umbilical PCB** |
| M3x8 BHCS | 2 | |
| M3x6 BHCS | 2 | |
| **Additional Parts for CAN Toolheads** |
| M3x6 BHCS | 4 | |

## Images

### Standard

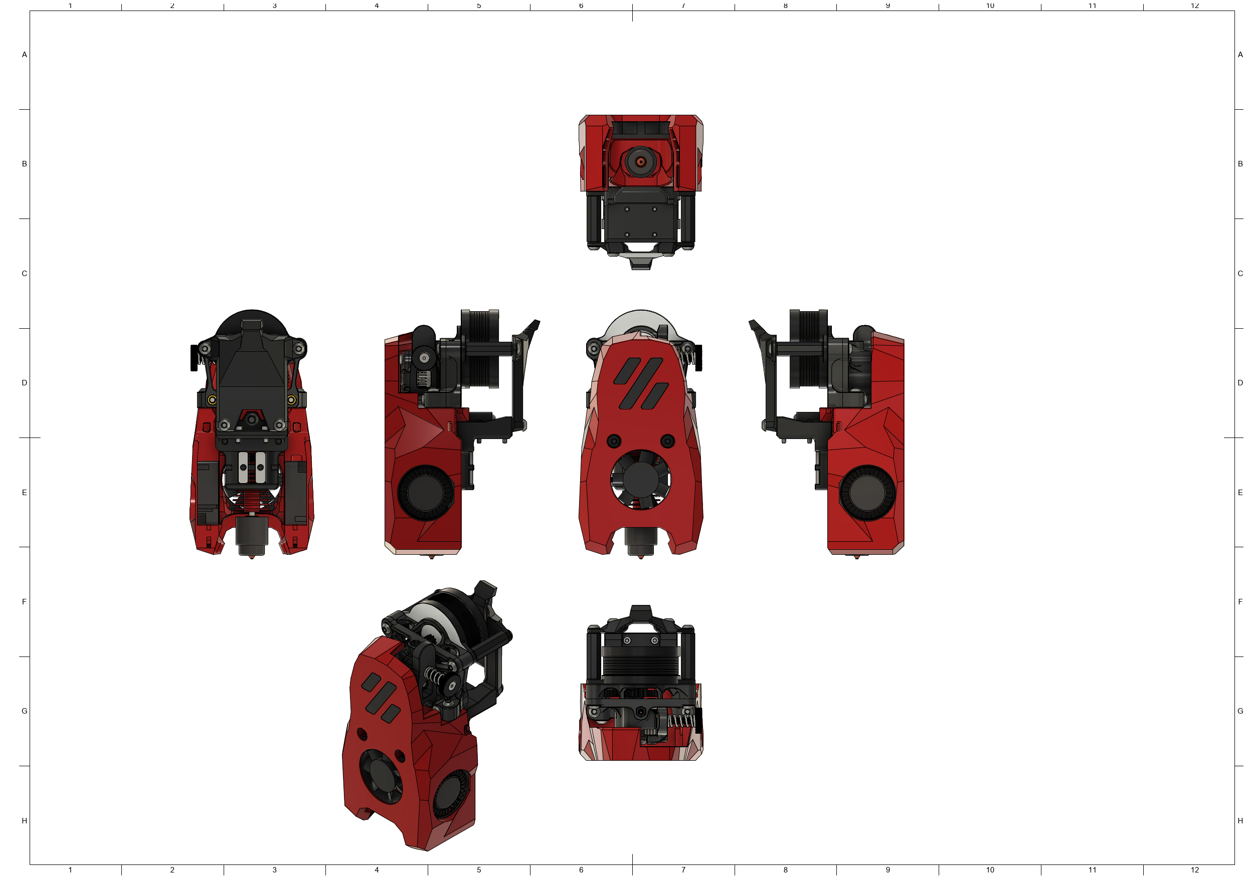
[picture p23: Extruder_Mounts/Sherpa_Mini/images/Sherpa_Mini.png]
Standard


### Minified

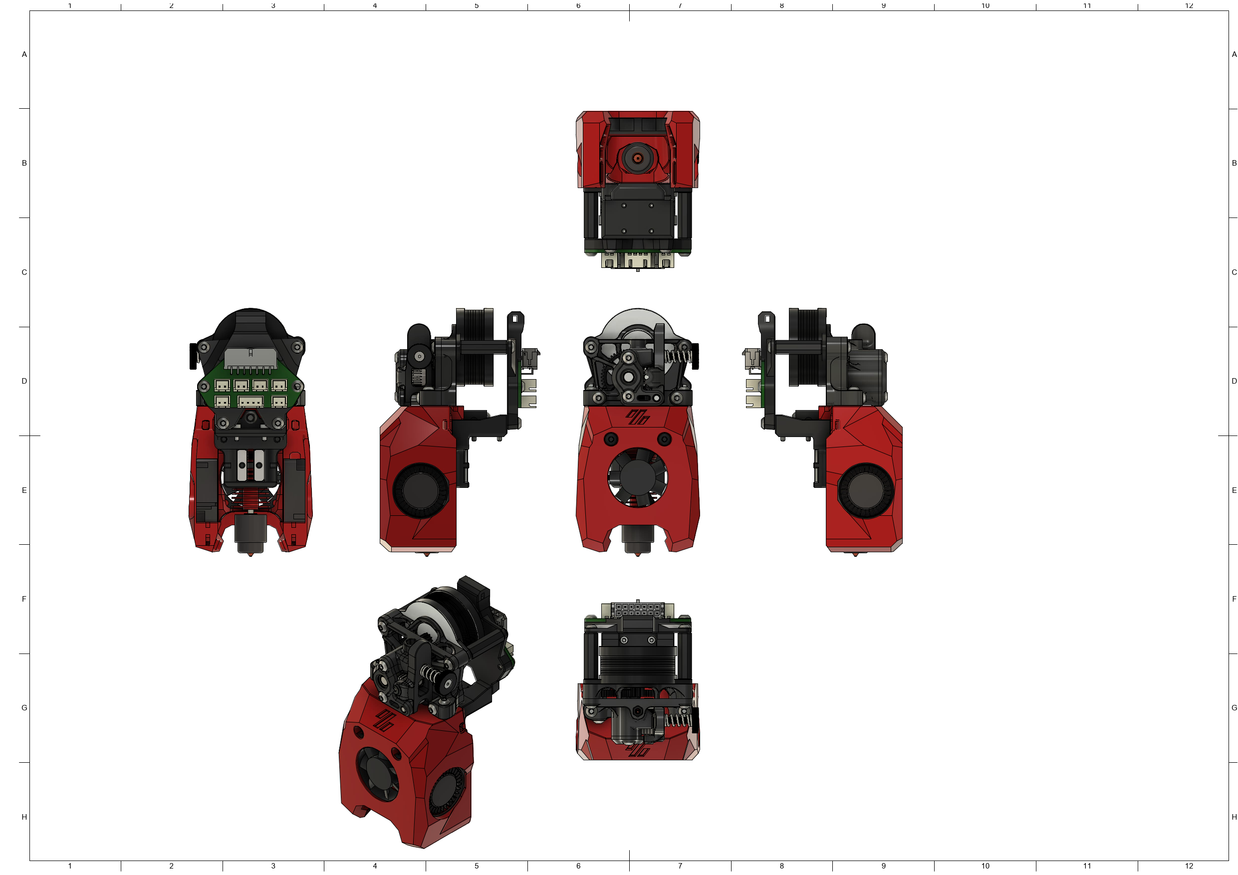
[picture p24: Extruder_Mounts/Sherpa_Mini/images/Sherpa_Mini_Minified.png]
Minified


## CAD-Source

The source for the CAD-File of the extruder is the [Sherpa Mini GitHub repository](https://github.com/Annex-Engineering/Sherpa_Mini-Extruder)

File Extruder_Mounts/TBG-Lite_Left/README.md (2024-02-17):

# MiniSB TBG-Lite Left

## PTFE-Holder

The TBG-Lite doesn't hold a PTFE-Reverse Bowden tube by itself, for this the PTFE-Holder is included. Mount by removing the top-right Screw and pushing on the PTFE-Holder and then securing it with a M3x30 BHCS.

The orientation in which the PTFE-Holder is printed makes it crucial that you have good layer adhesion. If you have issues with the part breaking during installation try printing it rotated by 90°, so the PTFE-Hole is at the top and the mounting holes at the bottom.

## BOM

| Part | Quantity | Notes |
| --- | --- | --- |
| M3x5x4 Heatset Insert | 4 |
| M3x35 BHCS | 2 | |
| M3x30 BHCS | 1 | Replace Screw for PTFE-Holder |
| M3x20 BHCS | 1 | |
| M3x12 BHCS | 3 |
| M3x6 BHCS | 2 |
| M3x8 FHCS | 1 |
| M3 Hex nut | 1 |
| 3010 Axial Fan | 1 |
| 3010 Blower Fan | 2 |
| Hotend | 1 | There are a number of supported Hotends, check the V0.2 GitHub for options |
| TBG-Lite Left Extruder | 1 |
| | | |
| **Additional Parts for standard strain relief** |
| M3x8 BHCS | 2 | |
| **Additional Parts for Umbilical PCB** |
| M3x8 BHCS | 2 | |
| M3x6 BHCS | 2 | |
| **Additional Parts for CAN Toolheads** |
| M3x6 BHCS | 4 | |

## Images

### Standard

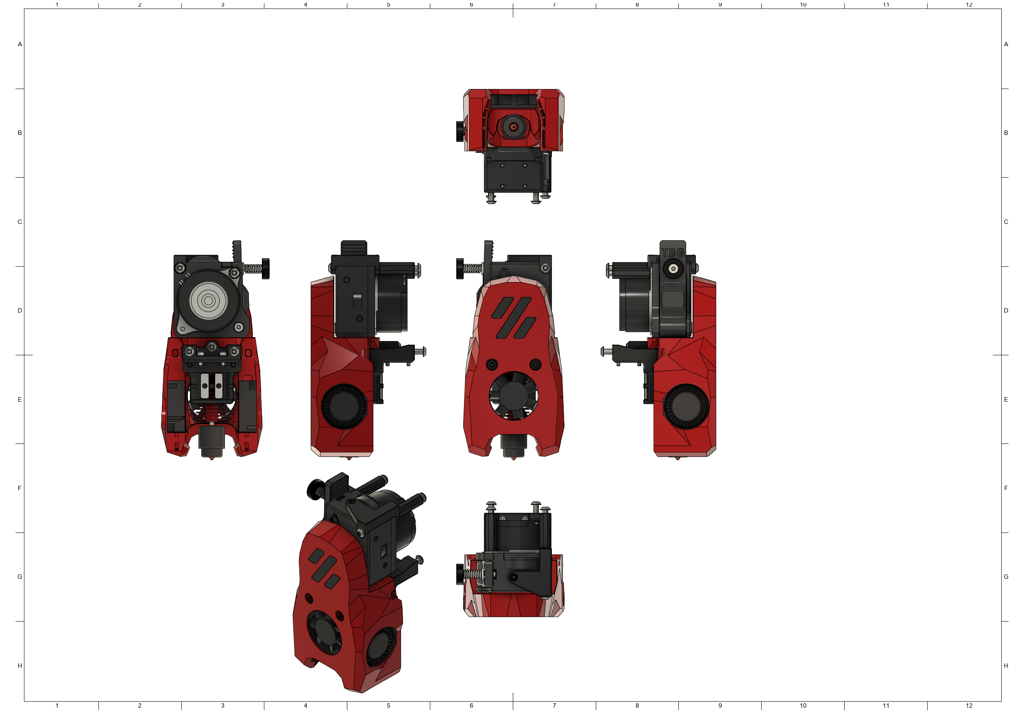
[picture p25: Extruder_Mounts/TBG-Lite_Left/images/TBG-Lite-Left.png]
Standard


### Minified

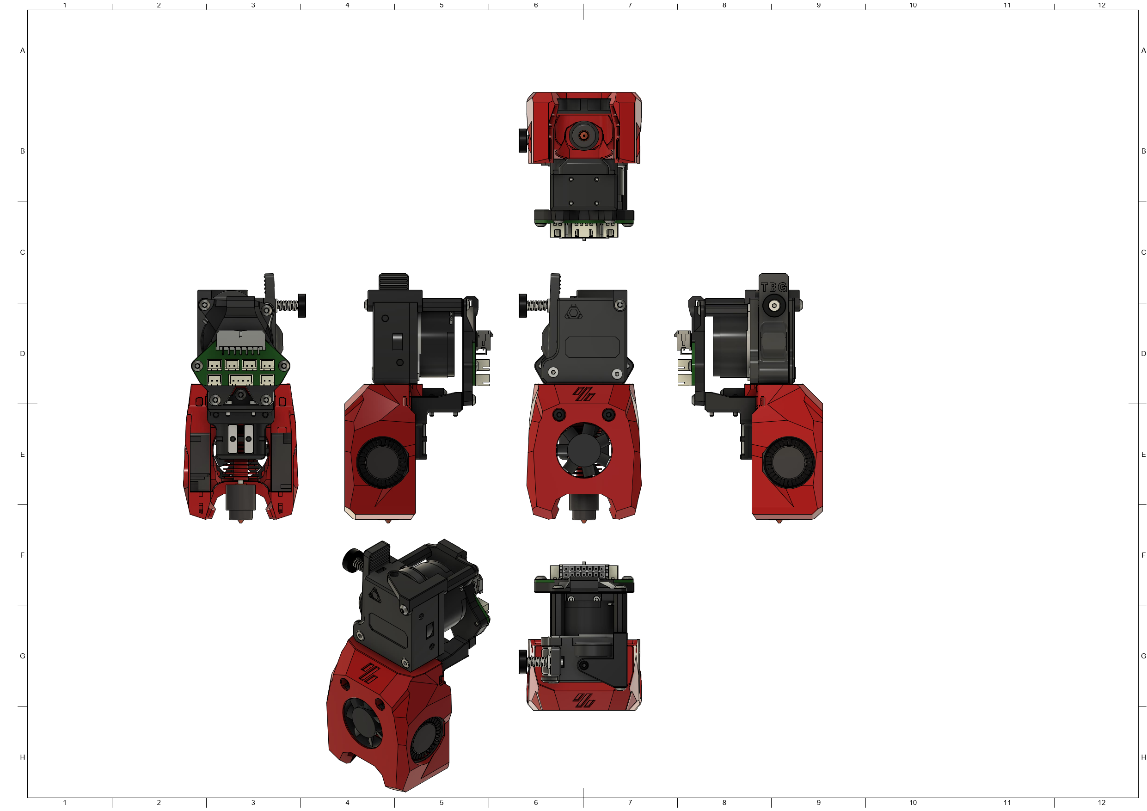
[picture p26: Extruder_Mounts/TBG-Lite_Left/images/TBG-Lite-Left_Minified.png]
Minified


## CAD-Source

The source for the CAD-File of the extruder is the [TriangleLab Google Drive](https://drive.google.com/drive/folders/1Wax49gipz4rJb-TFV5nfNy9x6yN46WqA)

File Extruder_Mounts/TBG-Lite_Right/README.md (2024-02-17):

# MiniSB TBG-Lite Right

## PTFE-Holder

The TBG-Lite doesn't hold a PTFE-Reverse Bowden tube by itself, for this the PTFE-Holder is included. Mount by removing the top-left Screw and pushing on the PTFE-Holder and then securing it with a M3x30 BHCS.

The orientation in which the PTFE-Holder is printed makes it crucial that you have good layer adhesion. If you have issues with the part breaking during installation try printing it rotated by 90°, so the PTFE-Hole is at the top and the mounting holes at the bottom.

## BOM

| Part | Quantity | Notes |
| --- | --- | --- |
| M3x5x4 Heatset Insert | 4 |
| M3x35 BHCS | 2 | |
| M3x30 BHCS | 1 | Replace Screw for PTFE-Holder |
| M3x20 BHCS | 1 | |
| M3x12 BHCS | 3 |
| M3x6 BHCS | 2 |
| M3x8 FHCS | 1 |
| M3 Hex nut | 1 |
| 3010 Axial Fan | 1 |
| 3010 Blower Fan | 2 |
| Hotend | 1 | There are a number of supported Hotends, check the V0.2 GitHub for options |
| TBG-Lite Right Extruder | 1 |
| | | |
| **Additional Parts for standard strain relief** |
| M3x8 BHCS | 2 | |
| **Additional Parts for Umbilical PCB** |
| M3x8 BHCS | 2 | |
| M3x6 BHCS | 2 | |
| **Additional Parts for CAN Toolheads** |
| M3x6 BHCS | 4 | |

## Images

### Standard

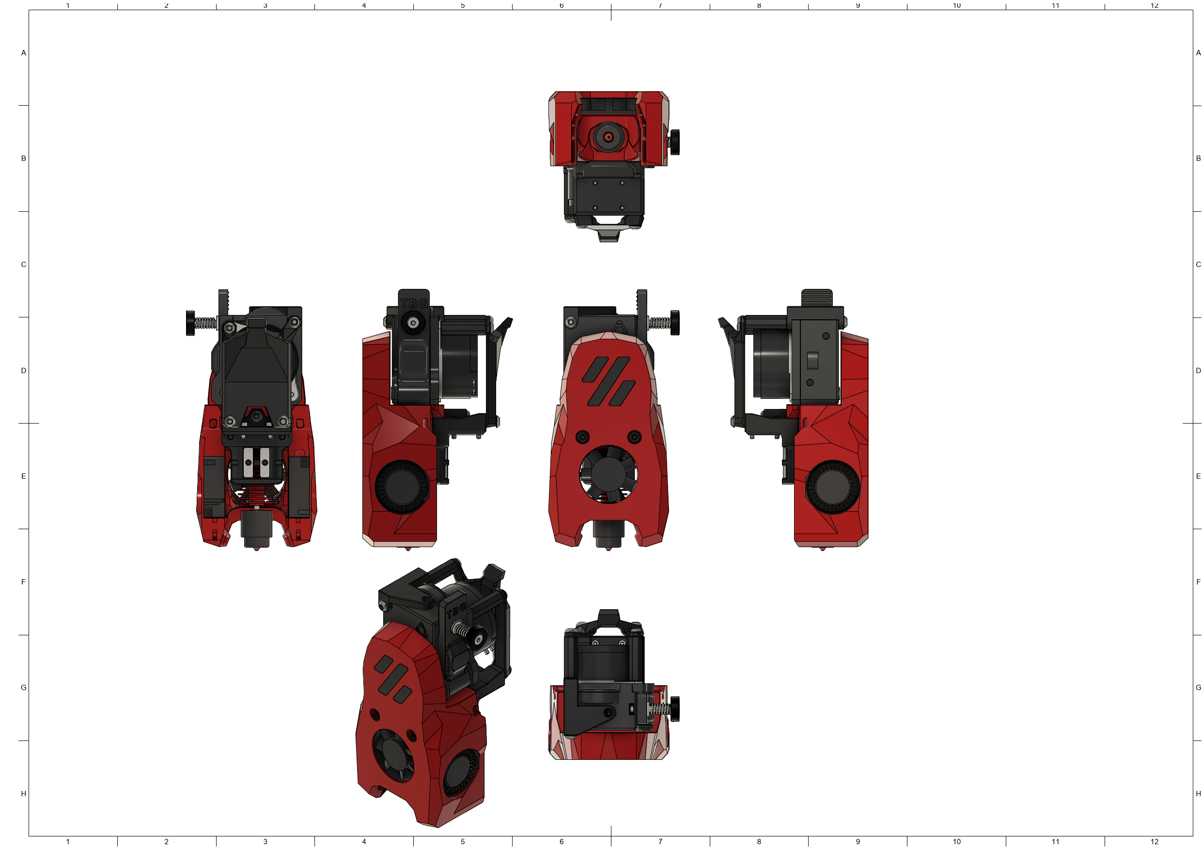
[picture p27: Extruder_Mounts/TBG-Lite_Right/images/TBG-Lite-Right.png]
Standard


### Minified

Minified

## CAD-Source

The source for the CAD-File of the extruder is the [TriangleLab Google Drive](https://drive.google.com/drive/folders/1Wax49gipz4rJb-TFV5nfNy9x6yN46WqA)

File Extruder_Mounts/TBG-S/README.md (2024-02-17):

# MiniSB TBG-S

## BOM

| Part | Quantity | Notes |
| --- | --- | --- |
| M3x5x4 Heatset Insert | 3 |
| M3x35 BHCS | 2 | |
| M3x20 BHCS | 1 | |
| M3x12 SHCS | 2 | Should be included with the TBG-S Extruder |
| M3x6 BHCS | 1 |
| M3 Hex nut | 1 |
| M2.5x10 SHCS | 1 |
| 3010 Axial Fan | 1 |
| 3010 Blower Fan | 2 |
| Hotend | 1 | There are a number of supported Hotends, check the V0.2 GitHub for options |
| TBG-S Extruder | 1 |
| | | |
| **Additional Parts for standard strain relief** |
| M3x8 BHCS | 2 | |
| **Additional Parts for Umbilical PCB** |
| M3x8 BHCS | 2 | |
| M3x6 BHCS | 2 | |
| **Additional Parts for CAN Toolheads** |
| M3x6 BHCS | 4 | |

## Images

### Standard

Standard

### Minified

Minified

## CAD-Source

The source for the CAD-File of the extruder is the [TriangleLab Google Drive](https://drive.google.com/drive/folders/1Wax49gipz4rJb-TFV5nfNy9x6yN46WqA)

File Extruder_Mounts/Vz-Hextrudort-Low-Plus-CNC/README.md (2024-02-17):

# MiniSB Vz-Hextrudort Low Plus CNC

## BOM

| Part | Quantity | Notes |
| --- | --- | --- |
| M3x5x4 Heatset Insert | 4 |
| M3x35 BHCS | 2 | |
| M3x20 BHCS | 1 |
| M3x16 BHCS | 1 | |
| M3x12 BHCS | 2 |
| M3x6 BHCS | 2 |
| M3 Hex nut | 1 |
| 3010 Axial Fan | 1 |
| 3010 Blower Fan | 2 |
| Hotend | 1 | There are a number of supported Hotends, check the V0.2 GitHub for options |
| Vz-Hextrudort Low Plus CNC Extruder | 1 |
| | | |
| **Additional Parts for standard strain relief** |
| M3x8 BHCS | 2 | |
| **Additional Parts for Umbilical PCB** |
| M3x8 BHCS | 2 | |
| M3x6 BHCS | 2 | |
| **Additional Parts for CAN Toolheads** |
| M3x6 BHCS | 4 | |

## Images

### Standard

Standard

### Minified

Minified

## CAD-Source

The source for the CAD-File of the extruder is the [Vz-HextrudORT GitHub repository](https://github.com/VzBoT3D/Vz-HextrudORT)

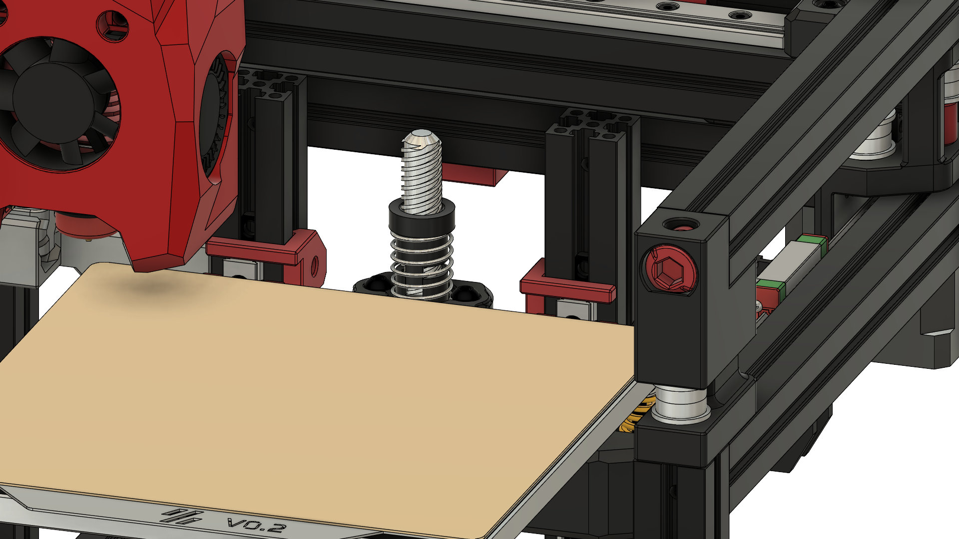
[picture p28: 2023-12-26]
Extruder_Mounts/_ZeroClick-Common/images/RailStoppers.png

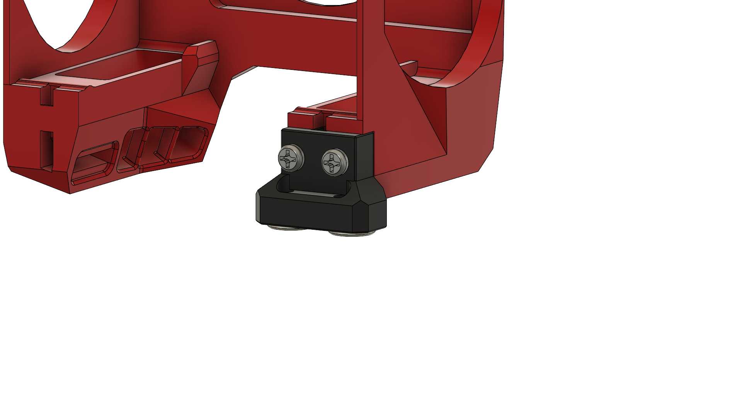
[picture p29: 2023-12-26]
Extruder_Mounts/_ZeroClick-Common/images/Mount.png

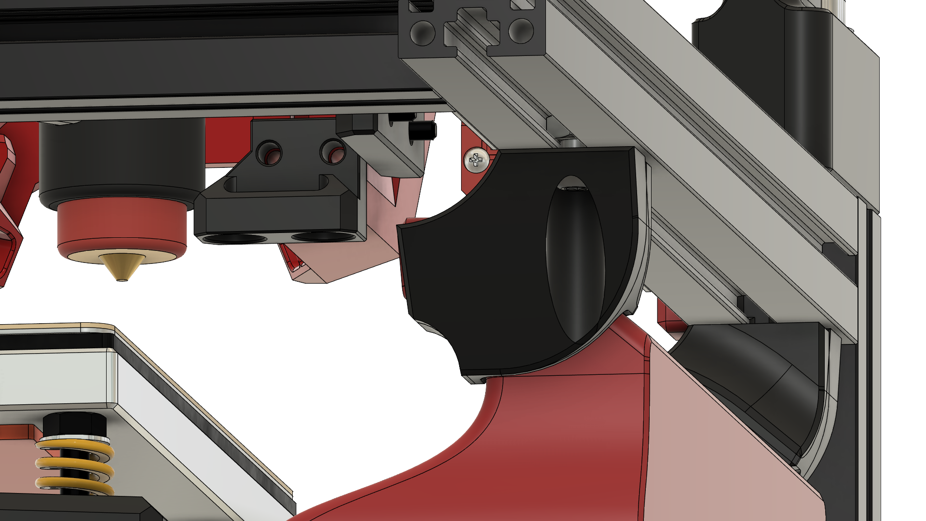
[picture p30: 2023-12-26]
Extruder_Mounts/_ZeroClick-Common/images/OffsetMount.png

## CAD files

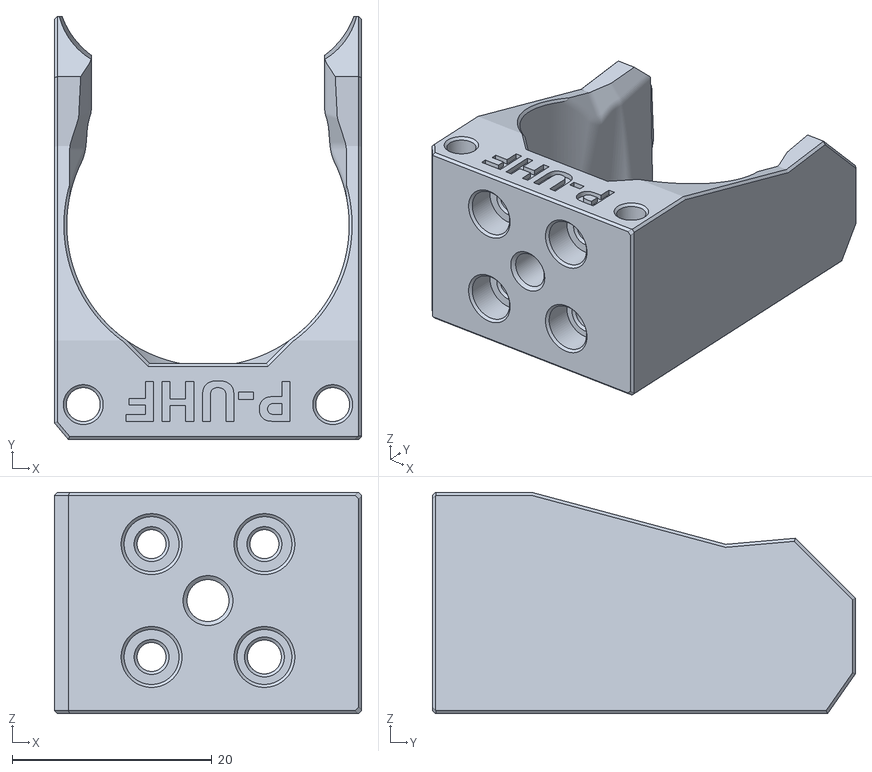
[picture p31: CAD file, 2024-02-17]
Extruder_Mounts/_Custom-Hotend-Mounts/STL/FS_Hotend_Mount_Dragon_UHF.stl
30.8 x 42.4 x 22.2

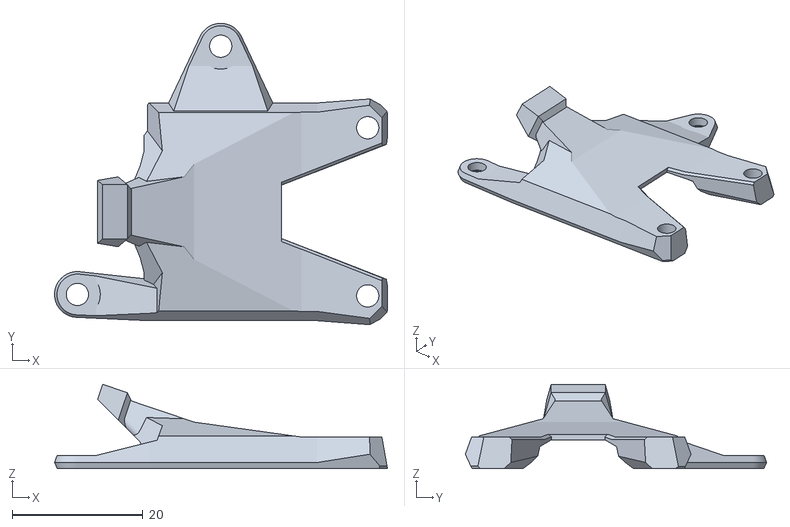
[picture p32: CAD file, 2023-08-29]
Extruder_Mounts/_OneFitsMost/STL/Adapter/Orbiter_v2.0/OFM_Strain_Relief_Plate_Orbiter-v2.0_x1.stl
50.9 x 46.1 x 12.9

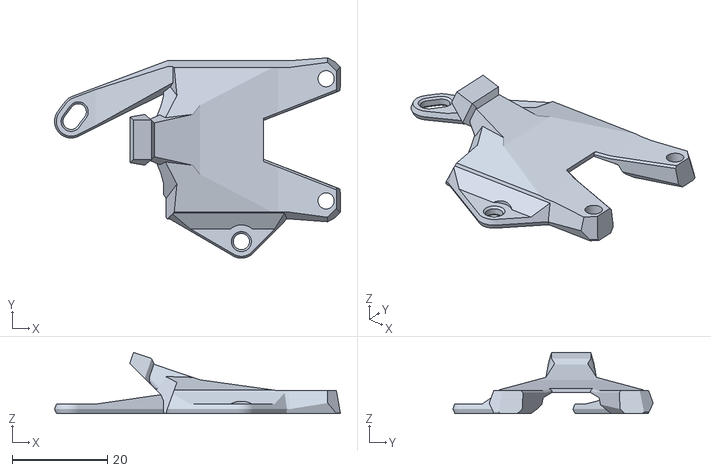
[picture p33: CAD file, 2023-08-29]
Extruder_Mounts/_OneFitsMost/STL/Adapter/Sherpa_Micro/OFM_Strain_Relief_Plate_Sherpa-Micro_x1.stl
60.2 x 42.2 x 12.9

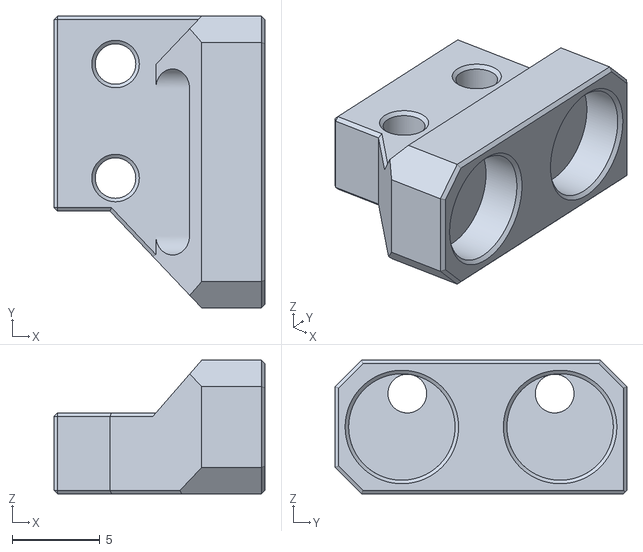
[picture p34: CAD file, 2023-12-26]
Extruder_Mounts/_ZeroClick-Common/STL/ZeroClick_Mount_Offset.stl
12.0 x 16.6 x 7.60

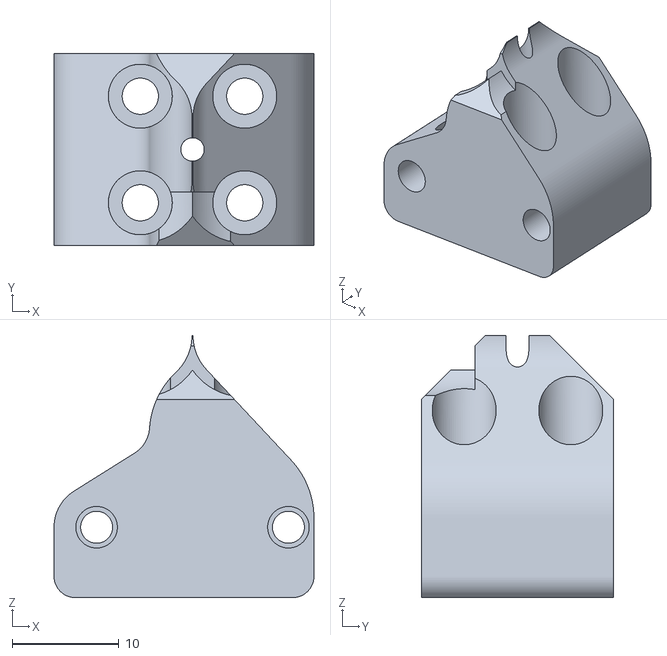
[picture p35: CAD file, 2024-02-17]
Extruder_Mounts/Apus/STL/Printed_Adapter_Apus_x1.stl
24.4 x 18.0 x 24.6

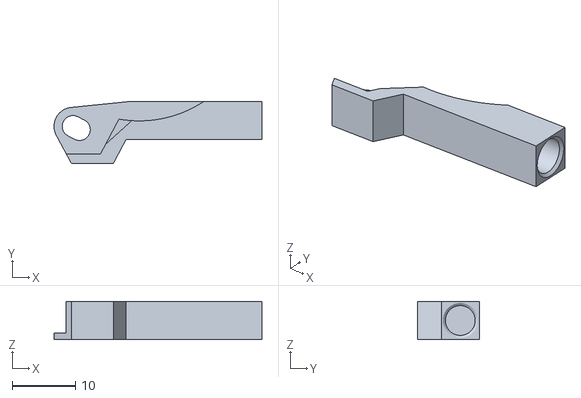
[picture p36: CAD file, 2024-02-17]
Extruder_Mounts/Apus/STL/Strain_Relief/Spacer/Spacer_Plate_Top_Right_Apus_x1.stl
32.8 x 9.73 x 6.00

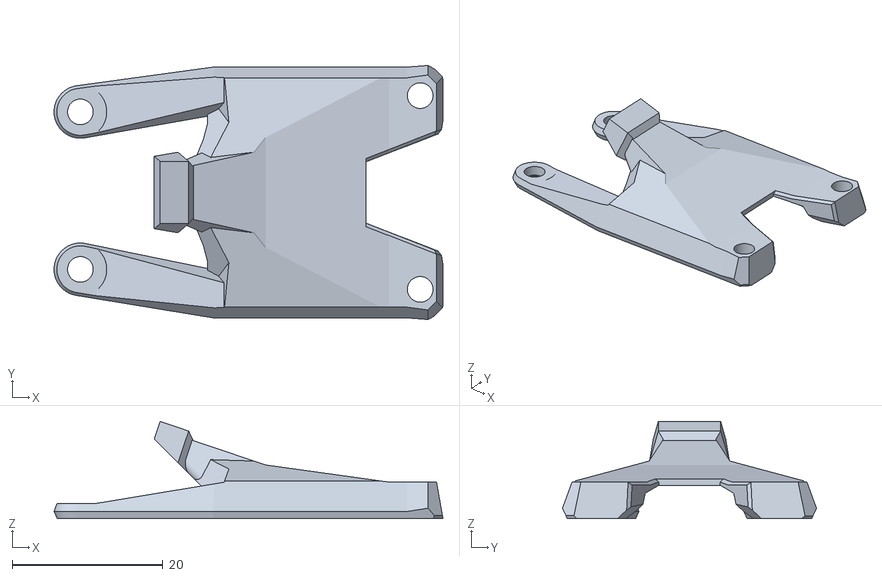
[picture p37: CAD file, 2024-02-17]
Extruder_Mounts/Apus/STL/Strain_Relief/Strain_Relief_Plate_Apus_x1.stl
51.6 x 33.7 x 12.9

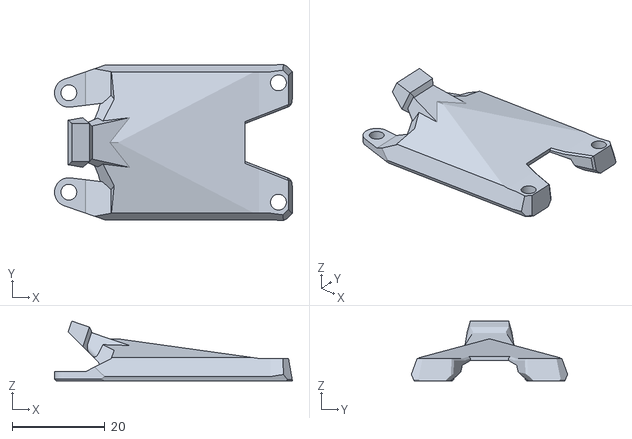
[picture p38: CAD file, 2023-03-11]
Extruder_Mounts/Apus/Strain_Relief_x1.stl
51.3 x 33.7 x 12.9

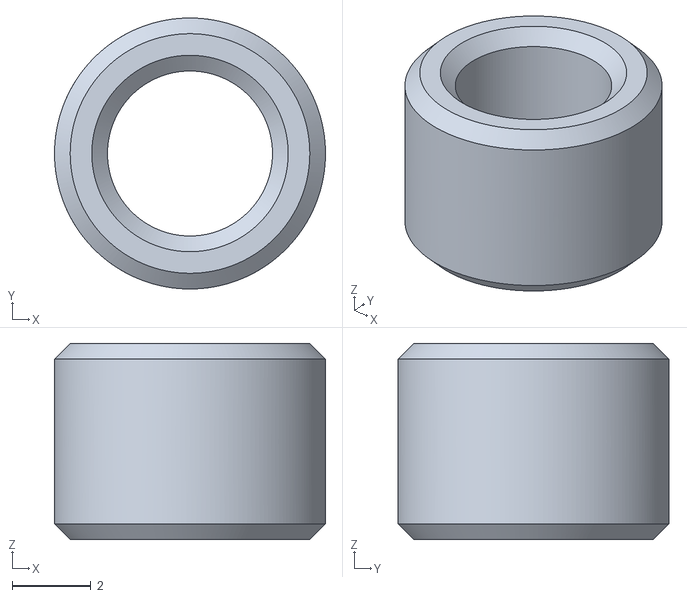
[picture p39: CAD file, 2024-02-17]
Extruder_Mounts/Aquarius/STL/PTFE-Guide_Aquarius_x1.stl
6.90 x 6.90 x 5.00

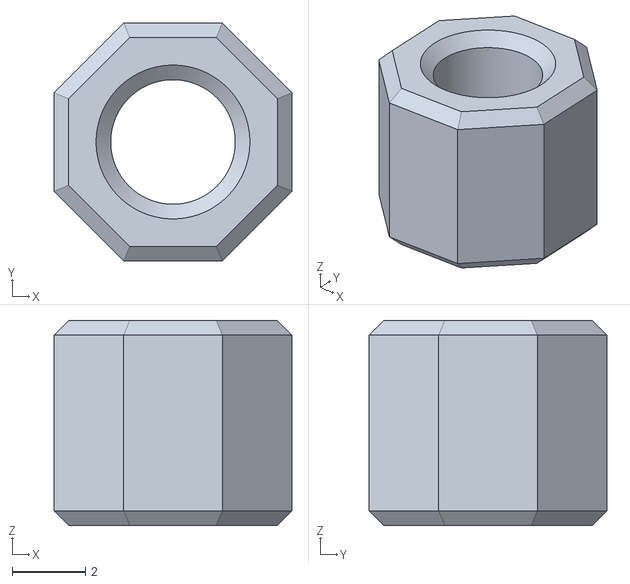
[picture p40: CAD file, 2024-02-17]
Extruder_Mounts/Aquarius/STL/Strain_Relief/Spacer/Spacer_Octagon_Aquarius_Stock_Motor_Bottom_x2.stl
6.50 x 6.50 x 5.60

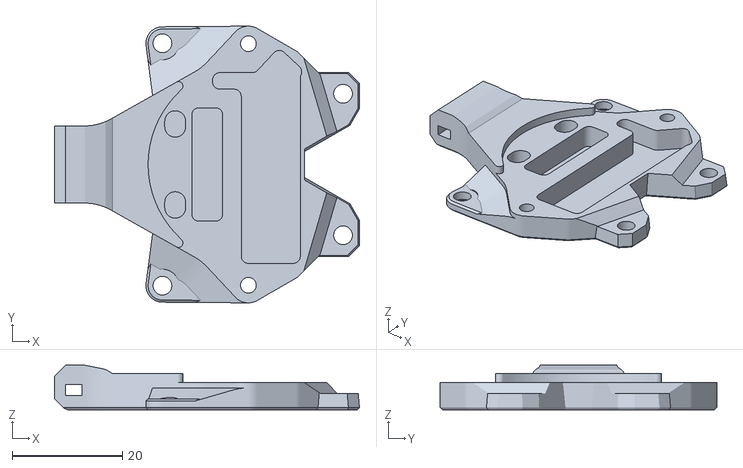
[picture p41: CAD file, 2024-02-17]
Extruder_Mounts/Aquarius/STL/Strain_Relief/Umbilical_Plate_Aquarius_x1.stl
55.4 x 50.2 x 8.10

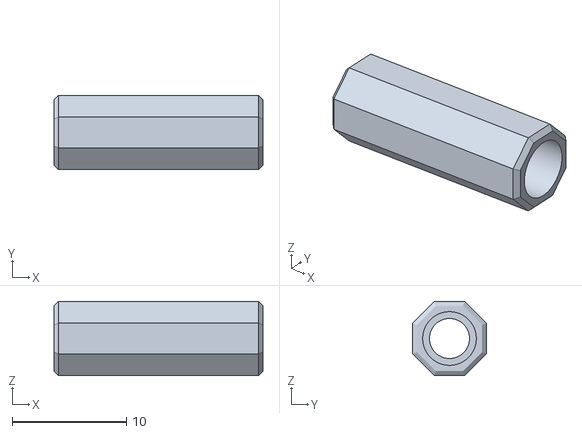
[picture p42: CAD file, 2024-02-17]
Extruder_Mounts/HGT/STL/Strain_Relief/Spacer/Spacer_Octagon_HGT_LDO_x1.stl
18.3 x 6.50 x 6.50

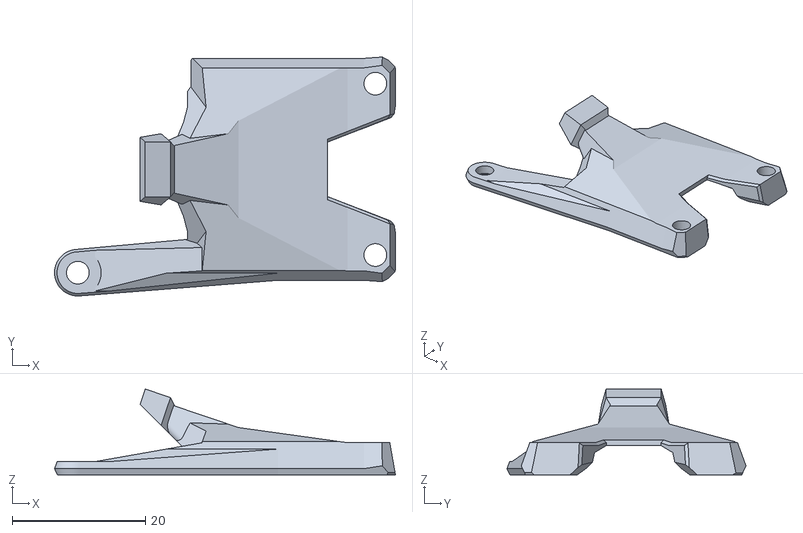
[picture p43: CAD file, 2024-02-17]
Extruder_Mounts/HGT/STL/Strain_Relief/Strain_Relief_Plate_HGT_x1.stl
51.1 x 35.9 x 12.9

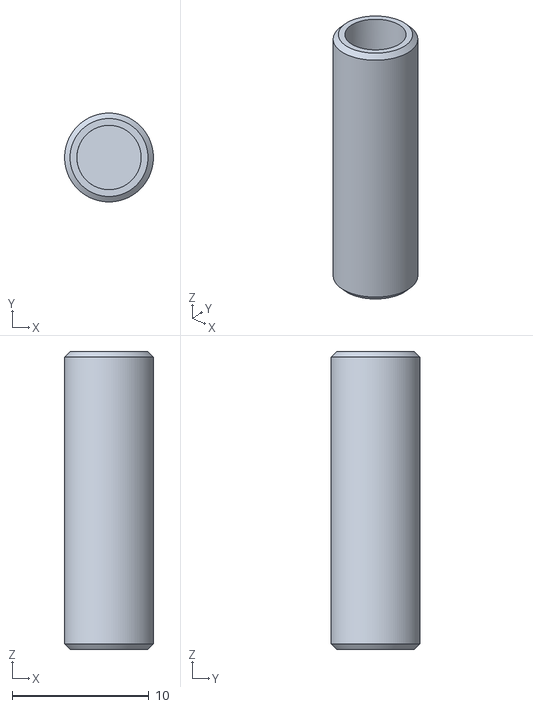
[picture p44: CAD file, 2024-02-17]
Extruder_Mounts/HGX-2.0/STL/Strain_Relief/Spacer/Spacer_Round_HGX-2.0_Moons_x1.stl
6.50 x 6.50 x 21.8

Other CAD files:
Extruder_Mounts/HGX-2.0/STL/Strain_Relief/Umbilical_Plate_HGX-2.0_x1.stl
Extruder_Mounts/HGX-Lite/STL/Strain_Relief/Spacer/Spacer_Octagon_HGX-Lite_Moons_x2.stl
Extruder_Mounts/HGX-Lite/STL/Strain_Relief/Strain_Relief_Plate_HGX-Lite_Shorter_Motor_x1.stl
Extruder_Mounts/LGX Lite/Umbilical_Plate_x1.stl
Extruder_Mounts/Apus/STL/Strain_Relief/CAN_Plate_Apus_x1.stl
Extruder_Mounts/Apus/STL/Strain_Relief/Spacer/Spacer_Plate_Bottom_Apus_x2.stl
Extruder_Mounts/Apus/STL/Strain_Relief/Spacer/Spacer_Plate_Top_Left_Apus_x1.stl
Extruder_Mounts/Apus/STL/Strain_Relief/Umbilical_Plate_Apus_x1.stl
Extruder_Mounts/Apus/Umbilical_Plate_x1.stl
Extruder_Mounts/Aquarius/STL/Strain_Relief/CAN_Plate_Aquarius_x1.stl
Extruder_Mounts/Aquarius/STL/Strain_Relief/Spacer/Spacer_Octagon_Aquarius_LDO_x2.stl
Extruder_Mounts/Aquarius/STL/Strain_Relief/Spacer/Spacer_Octagon_Aquarius_MOONS_x2.stl
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

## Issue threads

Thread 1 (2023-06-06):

Rapido HF Mount

abstractFlo, 2023-06-06:
Hi, is it possible to create a Mount for the Rapdio HF too? I want the flexibility of this awesome MiniSB Extruder Mounts but i am using Rapido HF only in my printers :D

I hope this is possible 🙈  (i can do it in CAD too, but my experience is really low :D)

JackJack3231, 2023-06-06:
I just added experimental versions of the cowlings using a extended air duct.
[Experimental Cowlings](https://github.com/JackJack3231/MiniSB-Extruder-Mounts/tree/main/Extruder_Mounts/_Experimental/RapidoHF)

I have not tested as my Rapido is currently in my Trident and I won't have time for at least one week.
In CAD everything looks fine.
So use at your own risk and let me know if it works for you.

The CAD-Files are also included so if there are some small issues you can try adjusting it yourself.

Commit: 599134eb163cda3329875077b44283df158a68ee

abstractFlo, 2023-06-06:
Will test this :) thank you

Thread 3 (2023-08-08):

contact area of third carriage bolt not hexagonal

probably-Erwins-Cat, 2023-08-08:
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
 The contact area could be made hexagonal so it fits perfectly to the form of the x-carriage. Is there a reason why the hexagon was cut short here?

JackJack3231, 2023-08-17:
Added with d30720d95192b9bc3cdfc89e31ee7aa8b7fa5b88

Closed 2023-08-17.

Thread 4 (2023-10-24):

Support ZeroClick toolhead mount

hudrucan, 2023-10-24:
It's awesome project but it much be better if it's supported `ZeroClick` probe mount from this project: https://github.com/zruncho3d/ZeroClick

JackJack3231, 2023-10-29:
I looked at this in the past and still want to add support,
however currently I'm quite busy and I have no idea when I will find the time to work on this.

The1whokn0cks, 2023-11-10:
Also agree that this is a awesome project. It gives everyone options who doesn't love options. Sorry to hijack this topic but have you.ever.also thought about maybe having support for the klicky pcb as well? Would love to see a standard cowling with klicky pcb support.

https://www.printables.com/model/634341-voron-02-mini-sb-orbiter-20-with-klicky-pcb

I've only seen this, and while great, was looking for a full cowling like your standard STLs.

JackJack3231, 2023-12-26:
With 2104ac3fffd3c31f0a55fcf4bde86b1b38ce579d a first iteration of a ZeroClick-Implementation has been added.
All parts except the Probe have been remade and also require special cowlings.
See https://github.com/JackJack3231/MiniSB-Extruder-Mounts/tree/main/Extruder_Mounts/_ZeroClick-Common for more information.

Until I get confirmation that this is working I will leave this issue open.

hudrucan, 2024-01-25:
> With [2104ac3](https://github.com/JackJack3231/MiniSB-Extruder-Mounts/commit/2104ac3fffd3c31f0a55fcf4bde86b1b38ce579d) a first iteration of a ZeroClick-Implementation has been added. All parts except the Probe have been remade and also require special cowlings. See https://github.com/JackJack3231/MiniSB-Extruder-Mounts/tree/main/Extruder_Mounts/_ZeroClick-Common for more information.
>
> Until I get confirmation that this is working I will leave this issue open.

Cool, sorry for late response, I will try it soon

hudrucan, 2024-01-26:
@JackJack3231 it's working with offset version for aux fan mount on the left
Demo video below, thanks for your support. ❤️

https://github.com/JackJack3231/MiniSB-Extruder-Mounts/assets/64943146/58c689dd-c8a4-4233-990f-10c884d3c062

https://github.com/JackJack3231/MiniSB-Extruder-Mounts/assets/64943146/2e9bc00e-d49a-475d-becb-29f7da9e1d79

JackJack3231, 2024-01-26:
Great to hear!
I'll close this issue for now.

If someone encounters any problems with the ZeroClick implementation feel free to create a new issue.

Closed 2024-01-26.

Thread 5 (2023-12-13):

SuperPINDA mount

TheSiggiePop, 2023-12-13:
Hi,

thanks for the great design! To make nozzle-swaps a bit easier I have added a SuperPINDA probe. Would you be interested in including this in all schrouds?

Cheers,
Greg

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

JackJack3231, 2023-12-17:
I like the idea.
Yes I am interested in adding it as an option for all shrouds, however my time is quite limited currently so it will probably be a few months until I can start working on this.

TheSiggiePop, 2023-12-18:
Alright. If you get to it, do give me a shout. I can also send you a fusion file. It's a bit messy, but the design has been running reliably for a fair bit now.

JackJack3231, 2024-02-17:
Added PINDA / M8 Inductive Probe mounts with d1ec6958f66f737c1fd9276e2b123d68056034a7

I tested it in my printer and it seems to work.

Closing this issue for now.

Closed 2024-02-17.

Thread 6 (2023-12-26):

Klicky PCB Support

JackJack3231, 2023-12-26:
Also agree that this is a awesome project. It gives everyone options who doesn't love options. Sorry to hijack this topic but have you.ever.also thought about maybe having support for the klicky pcb as well? Would love to see a standard cowling with klicky pcb support.

https://www.printables.com/model/634341-voron-02-mini-sb-orbiter-20-with-klicky-pcb

I've only seen this, and while great, was looking for a full cowling like your standard STLs.

_Originally posted by @The1whokn0cks in https://github.com/JackJack3231/MiniSB-Extruder-Mounts/issues/4#issuecomment-1806231052_

JackJack3231, 2024-02-17:
Did some work on this, however I will stop for now as there are a lot of challenges with implementing this properly.

1. Because of the size of the PCB it will reach into the airpath and (slightly) obstruct it.
2. The PCB-Size and connector on top make it very difficult to fit in the v0 without collisions

The current version is in the CAD-Files, however I do not recommend using it, as there are collision issues from my testing.
If someone wants to use this as a basis for their work feel free.

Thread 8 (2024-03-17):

LGX Lite HF klicky cowling top screw position is off and did not work with 0.2r1 mount

ds4213, 2024-03-17:
thanks for your work and im trying to use the LGX Lite HF klicky cowling however the top screw was off and cannot fit to the 0.2r1 x mount.
found that the model is a little diferent as shown below
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
without klicky

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

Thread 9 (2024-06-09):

LGX Lite PINDA cowling top screw mount issue

kpe, 2024-06-09:
I'm trying to use the HGX Lite with a metal x carriage, however unlike most cowlings or the main HGX Lite, the PINDA one top screw is not flush with the hexagon (not sure how to word this), but here two screenshots
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

Maybe the change can be propagated from the base minified HGX Lite to the PINDA and the other variants.

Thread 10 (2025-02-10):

Rapido UHF mount

smarzony, 2025-02-10:
Hey, is this possible to adapt this project for Rapido UHF?
Here is a link to it: [Rapido UHF](https://www.phaetus.com/products/rapido-hotend)
I'm thinking about the one with [longer volcano-style nozzle](https://github.com/Phaetus/Rapido/blob/main/Product%20Wireframes/Rapido%20UHF%20wireframes.pdf)
Thank you for all this work, it's amazing.
If this is already here please exuce me, because I cannot find it. Especially interests me Sherpa Mini Pinda style.

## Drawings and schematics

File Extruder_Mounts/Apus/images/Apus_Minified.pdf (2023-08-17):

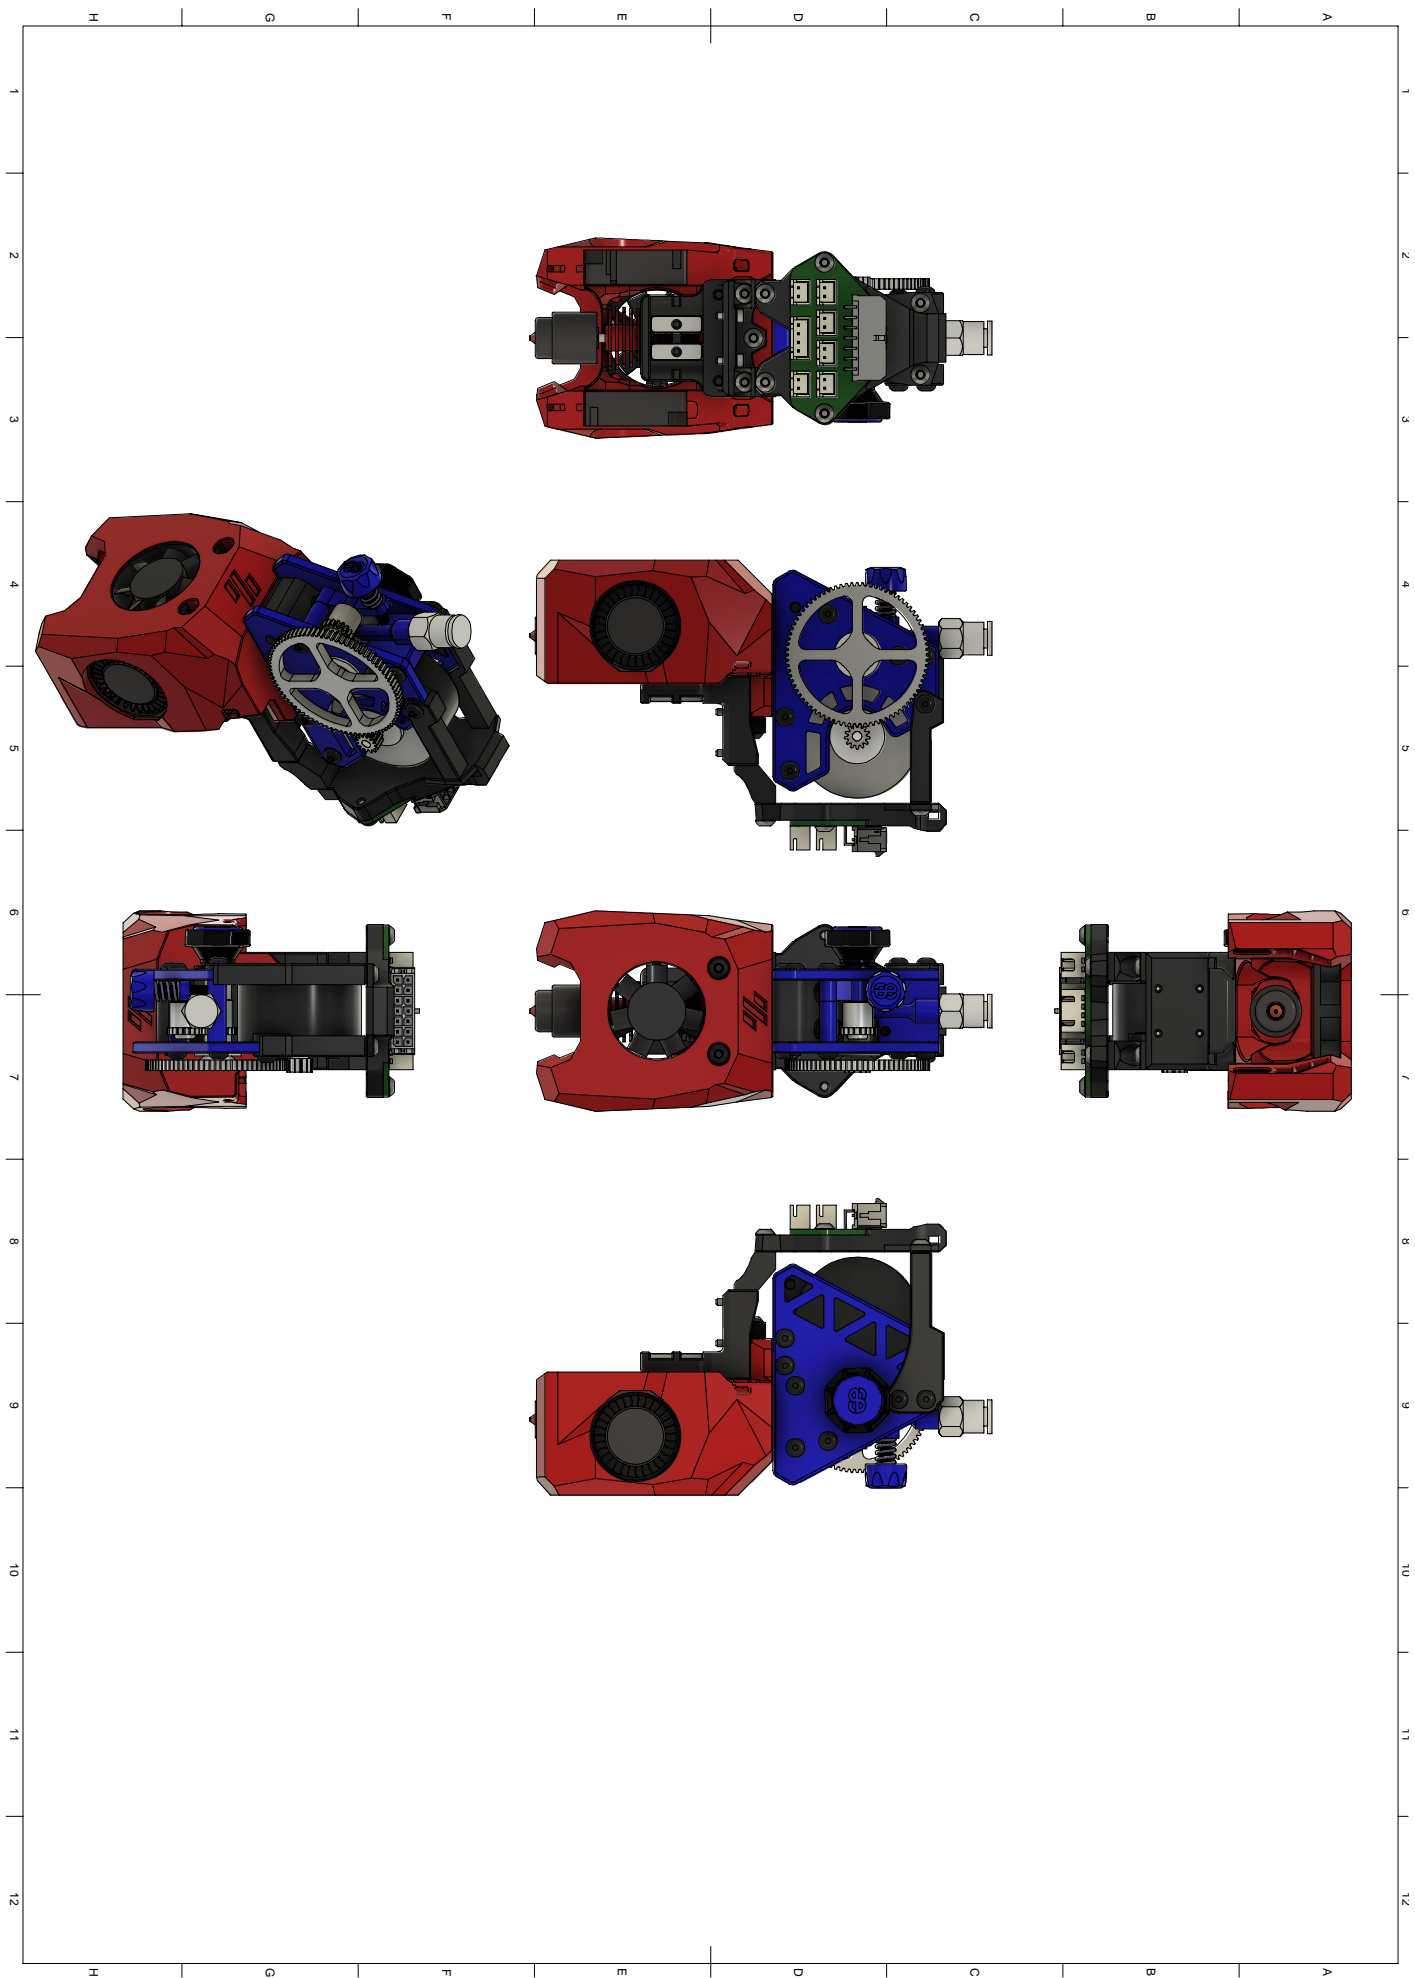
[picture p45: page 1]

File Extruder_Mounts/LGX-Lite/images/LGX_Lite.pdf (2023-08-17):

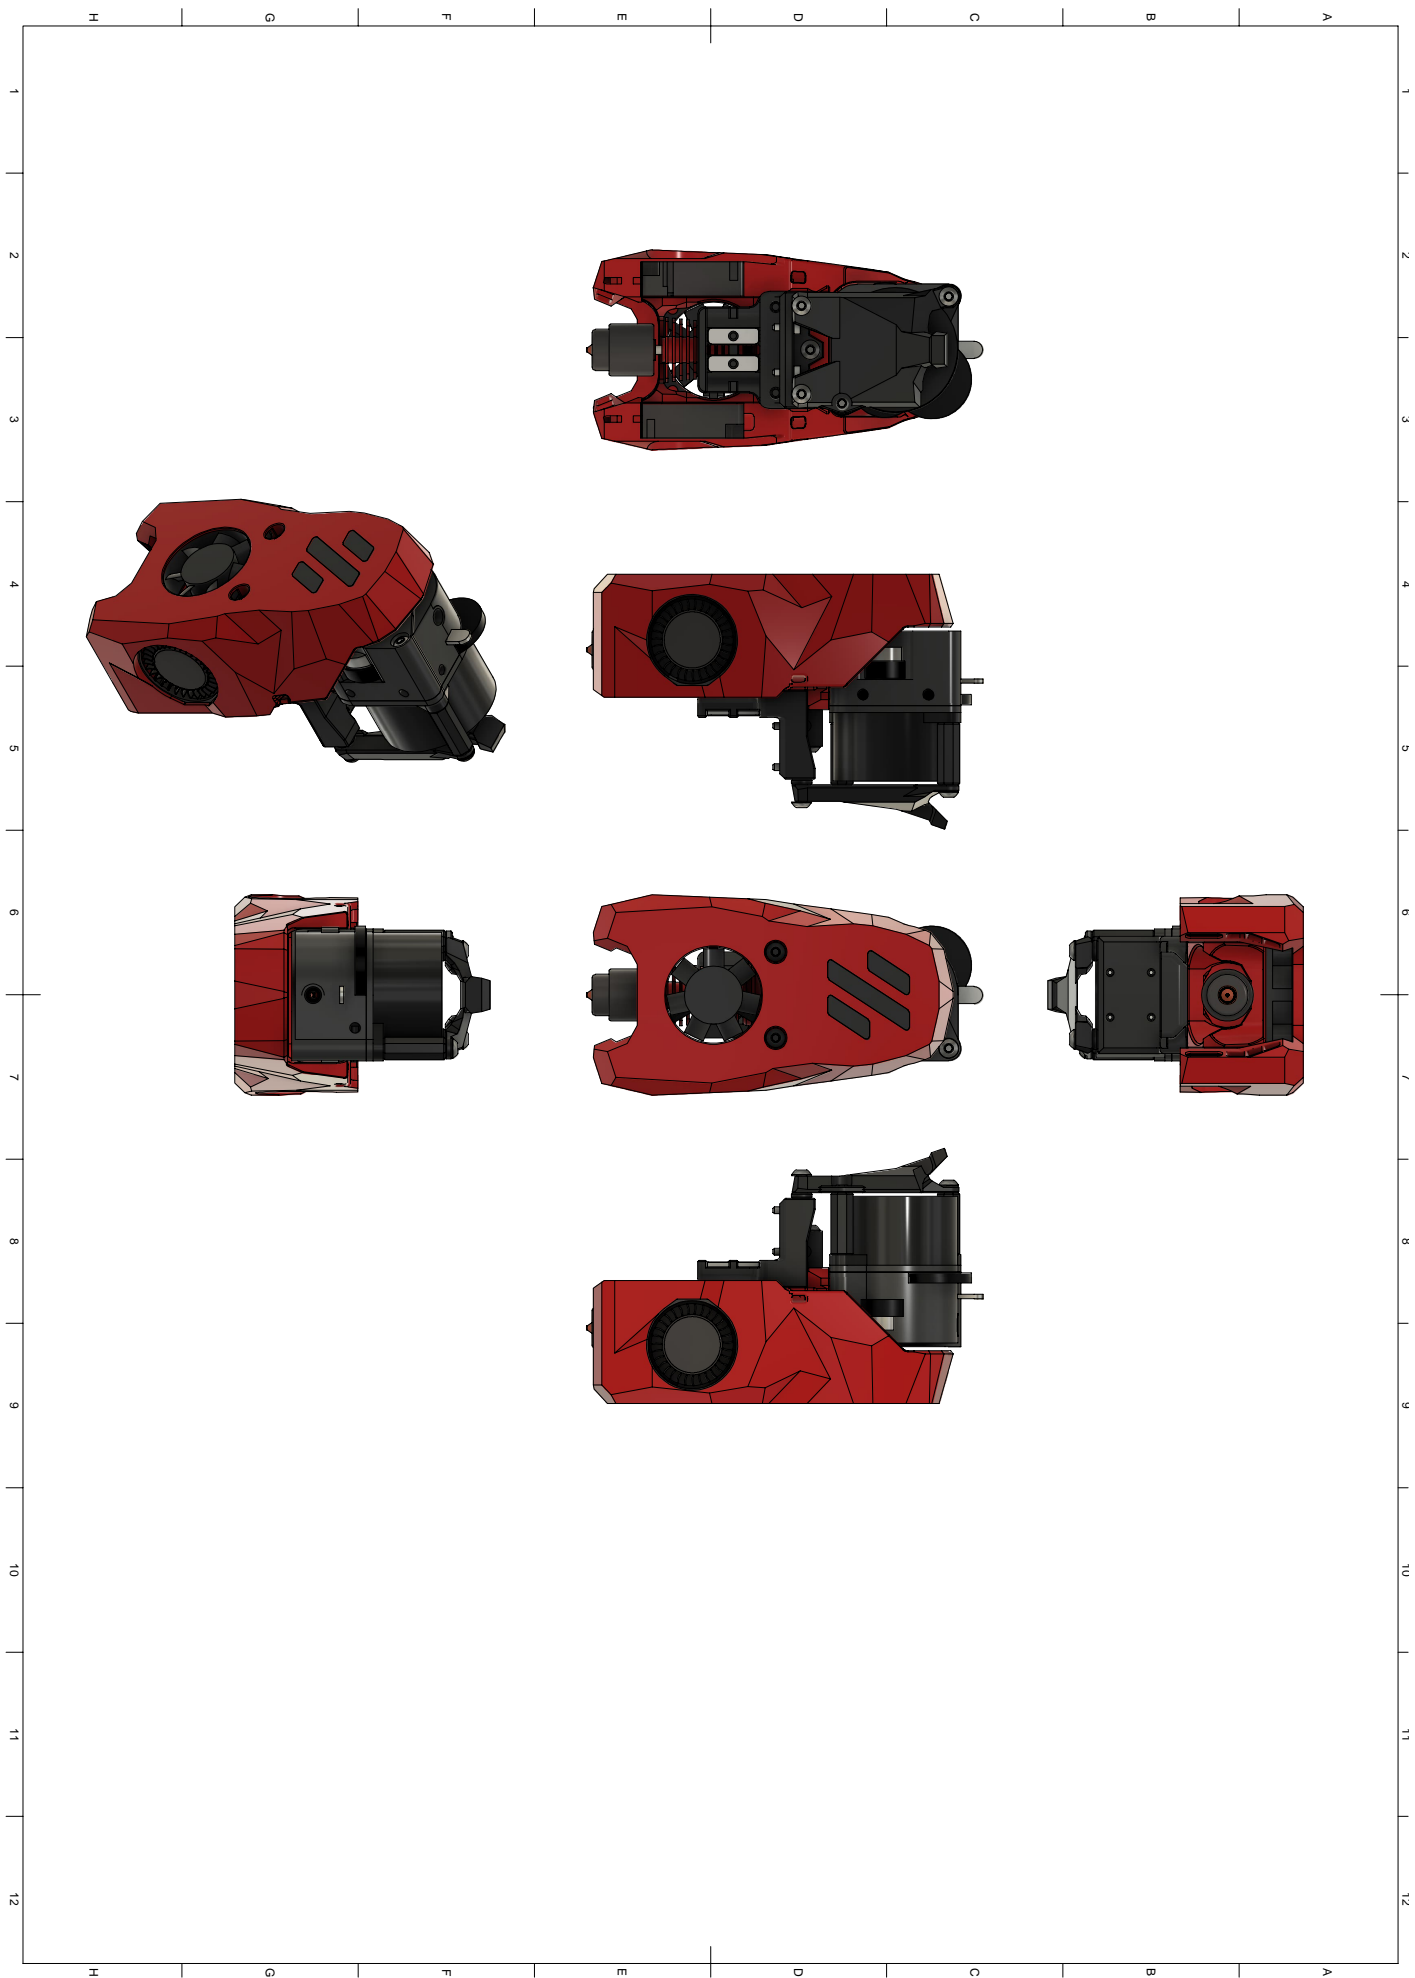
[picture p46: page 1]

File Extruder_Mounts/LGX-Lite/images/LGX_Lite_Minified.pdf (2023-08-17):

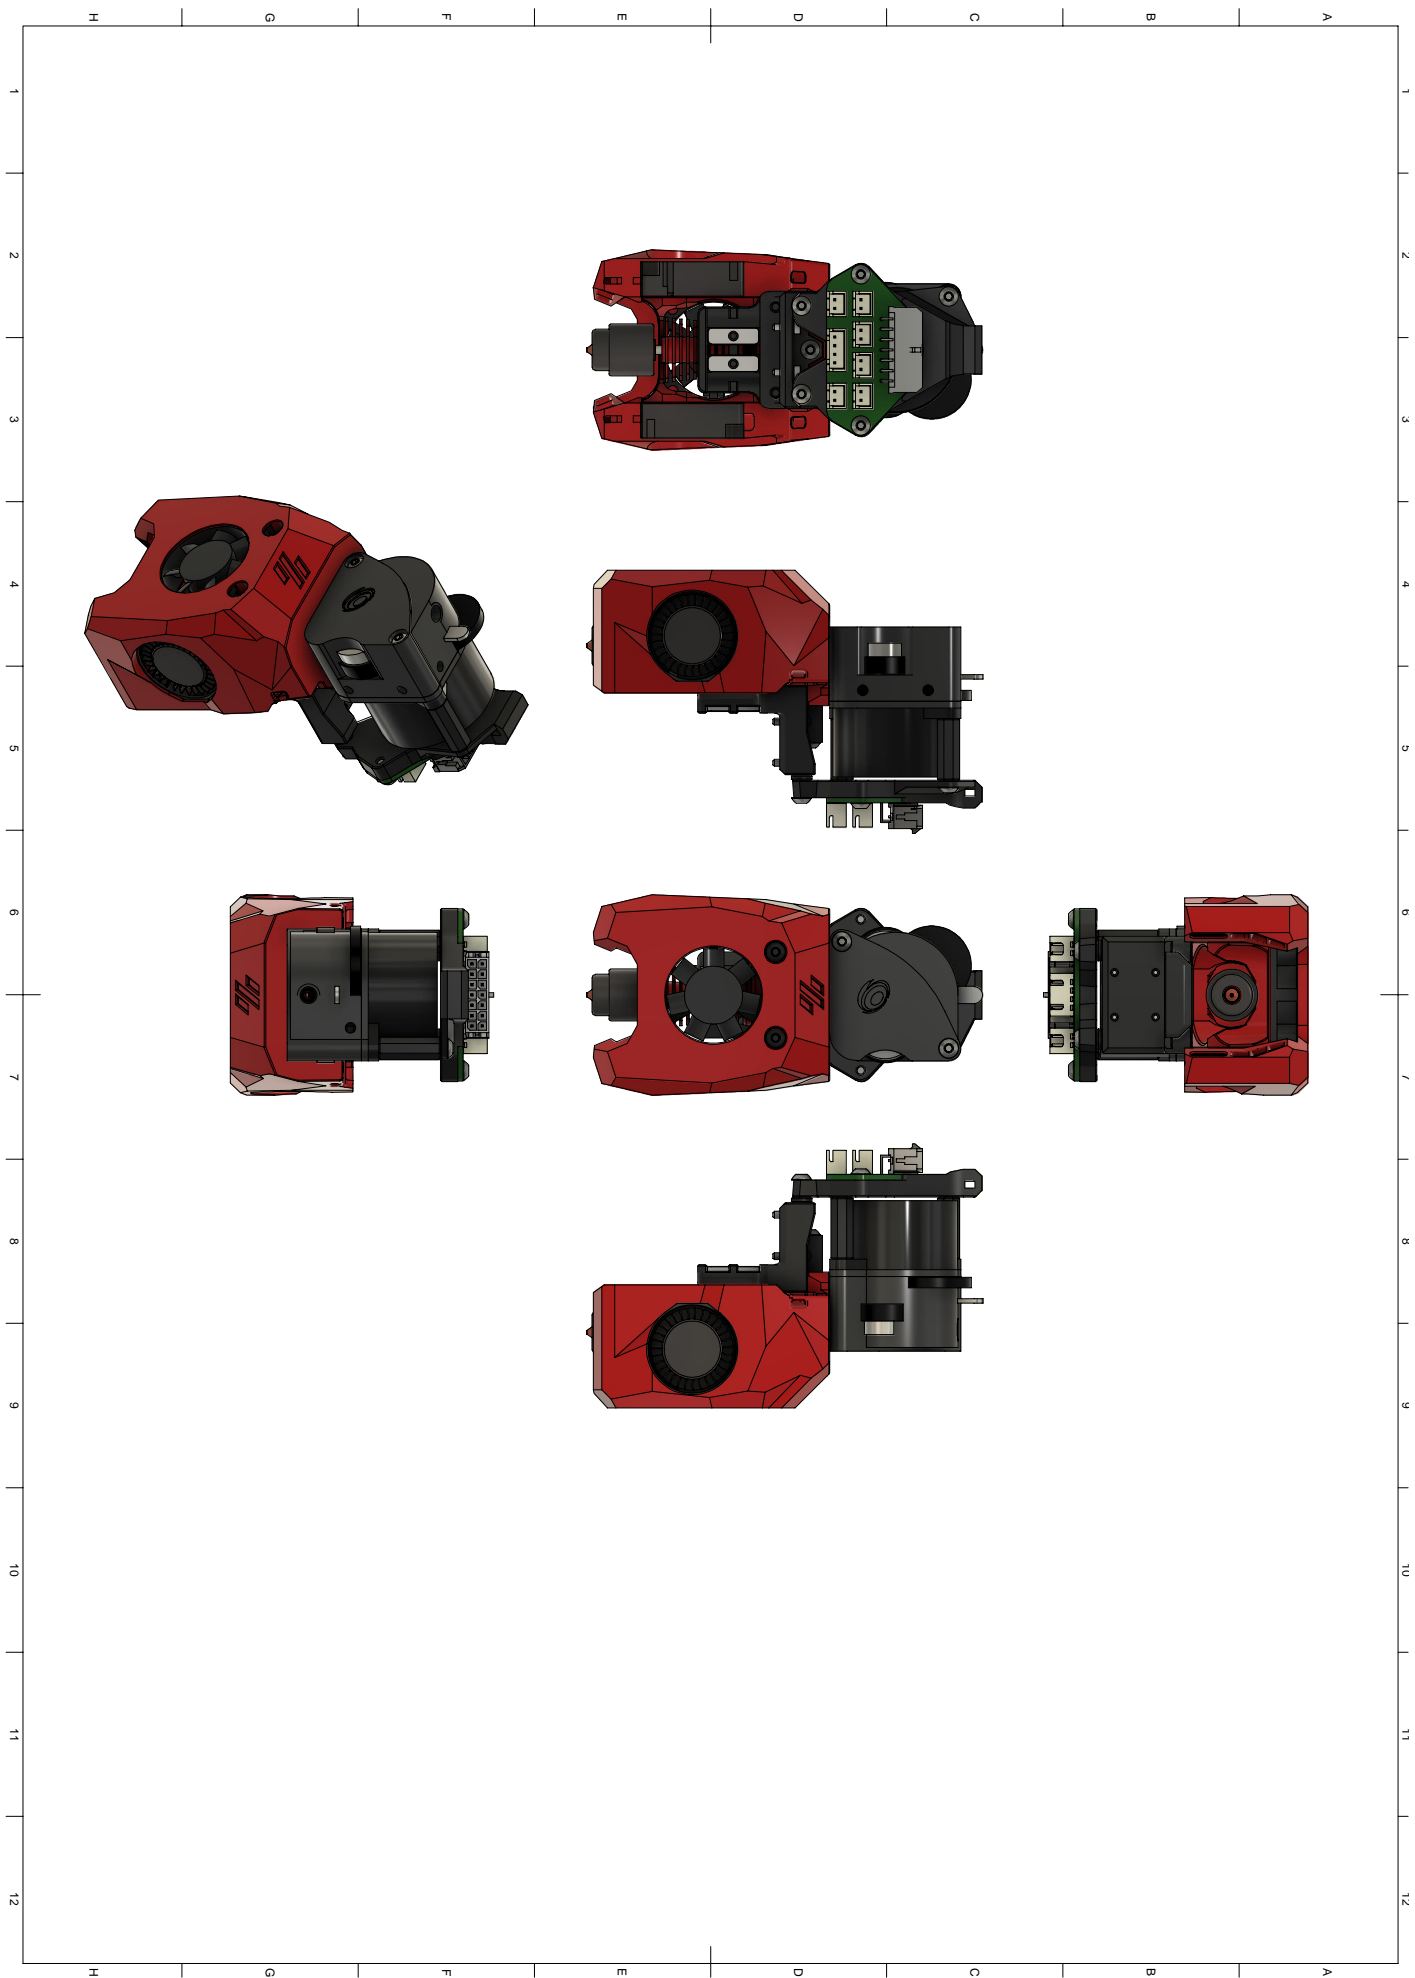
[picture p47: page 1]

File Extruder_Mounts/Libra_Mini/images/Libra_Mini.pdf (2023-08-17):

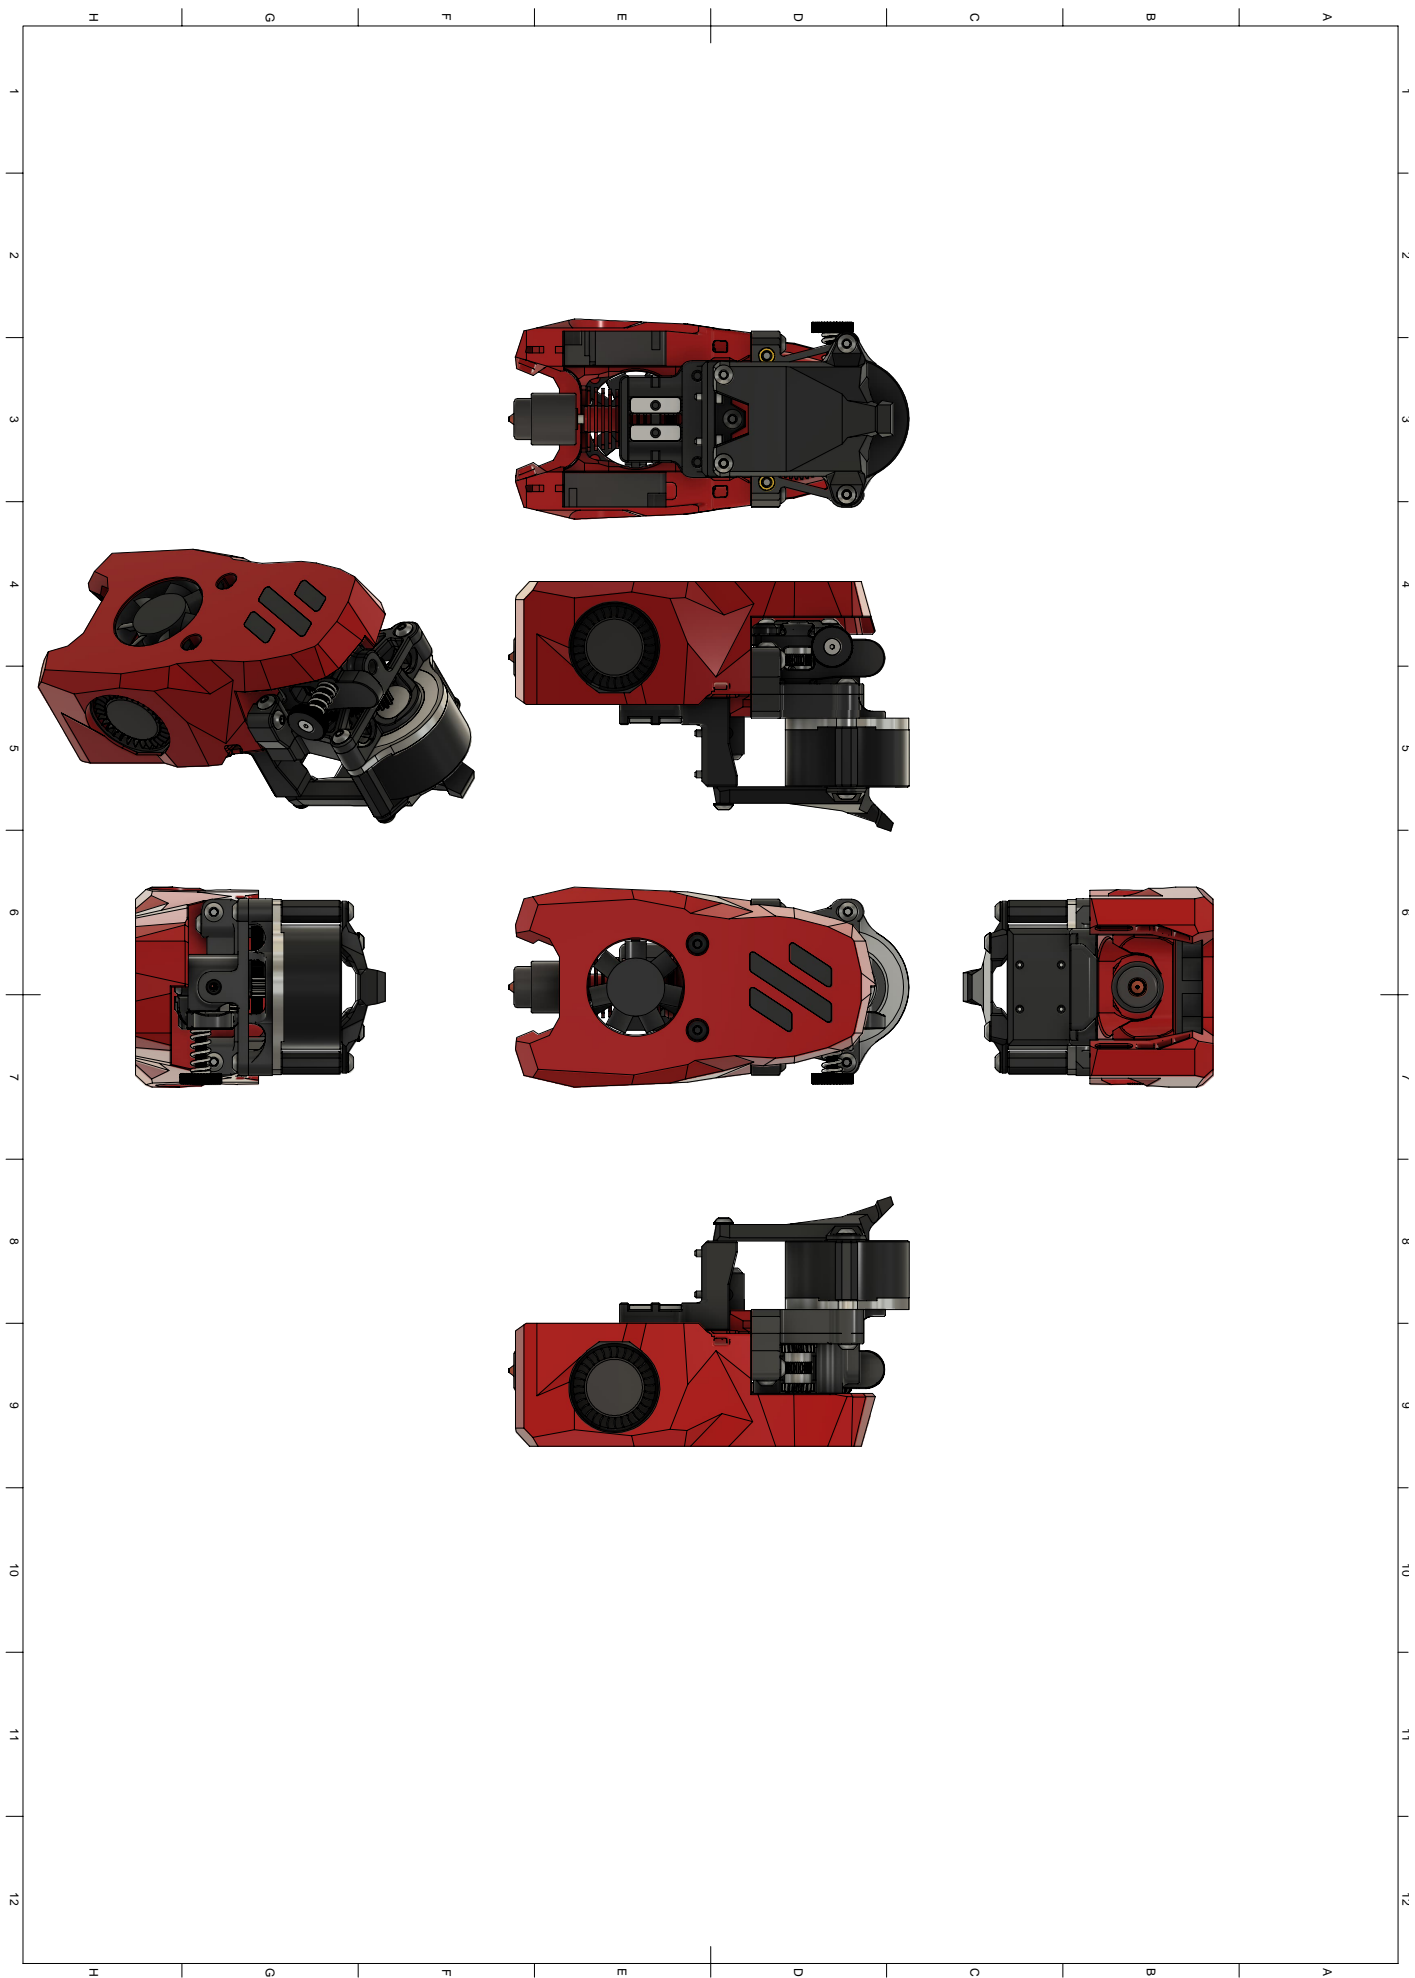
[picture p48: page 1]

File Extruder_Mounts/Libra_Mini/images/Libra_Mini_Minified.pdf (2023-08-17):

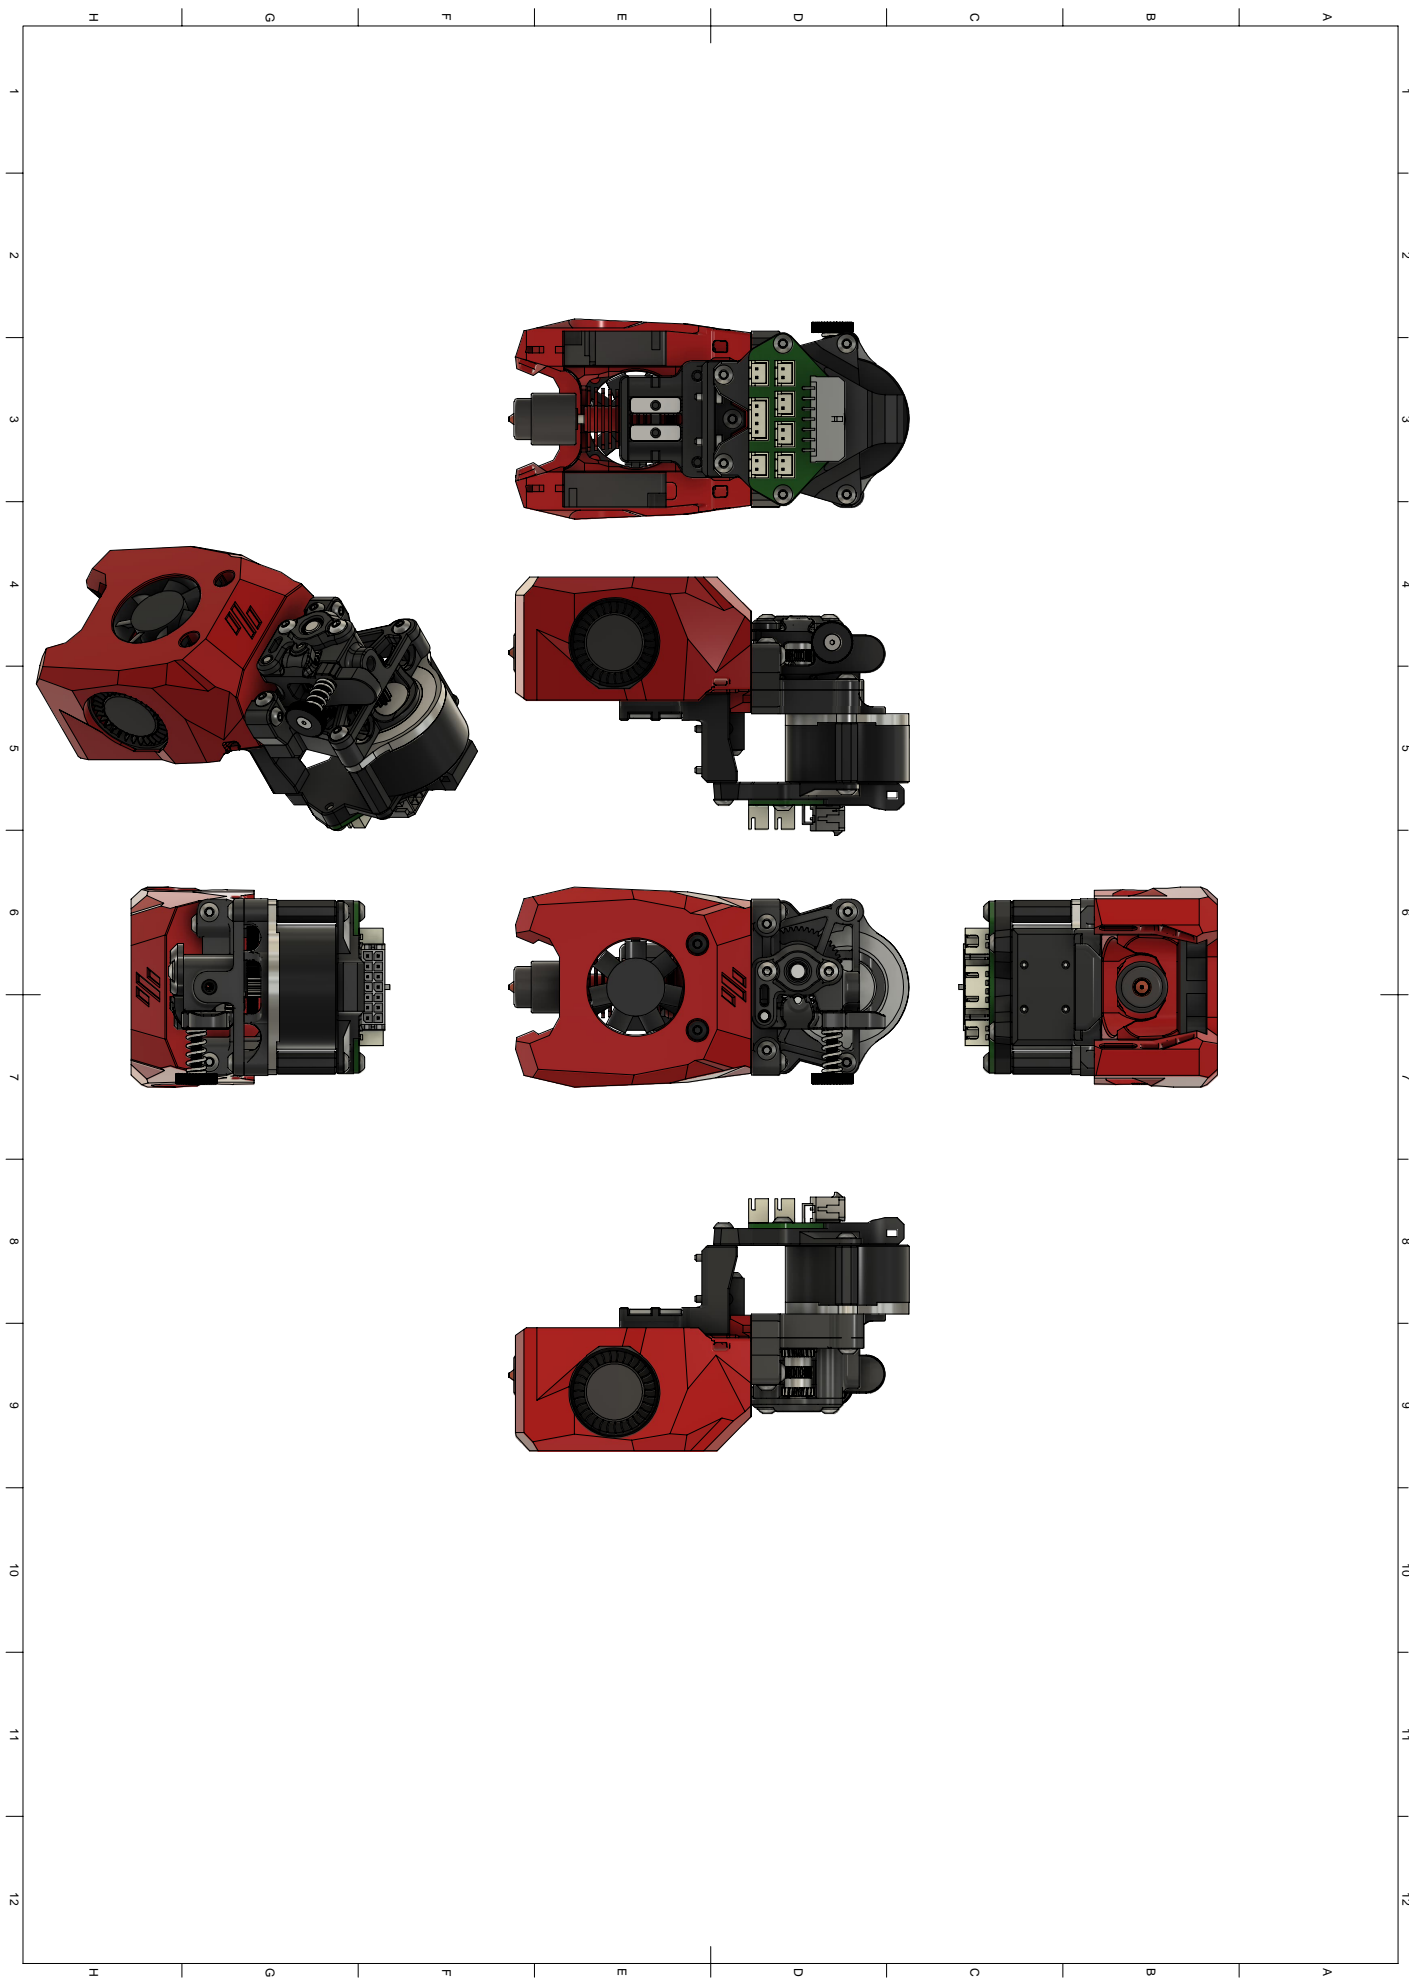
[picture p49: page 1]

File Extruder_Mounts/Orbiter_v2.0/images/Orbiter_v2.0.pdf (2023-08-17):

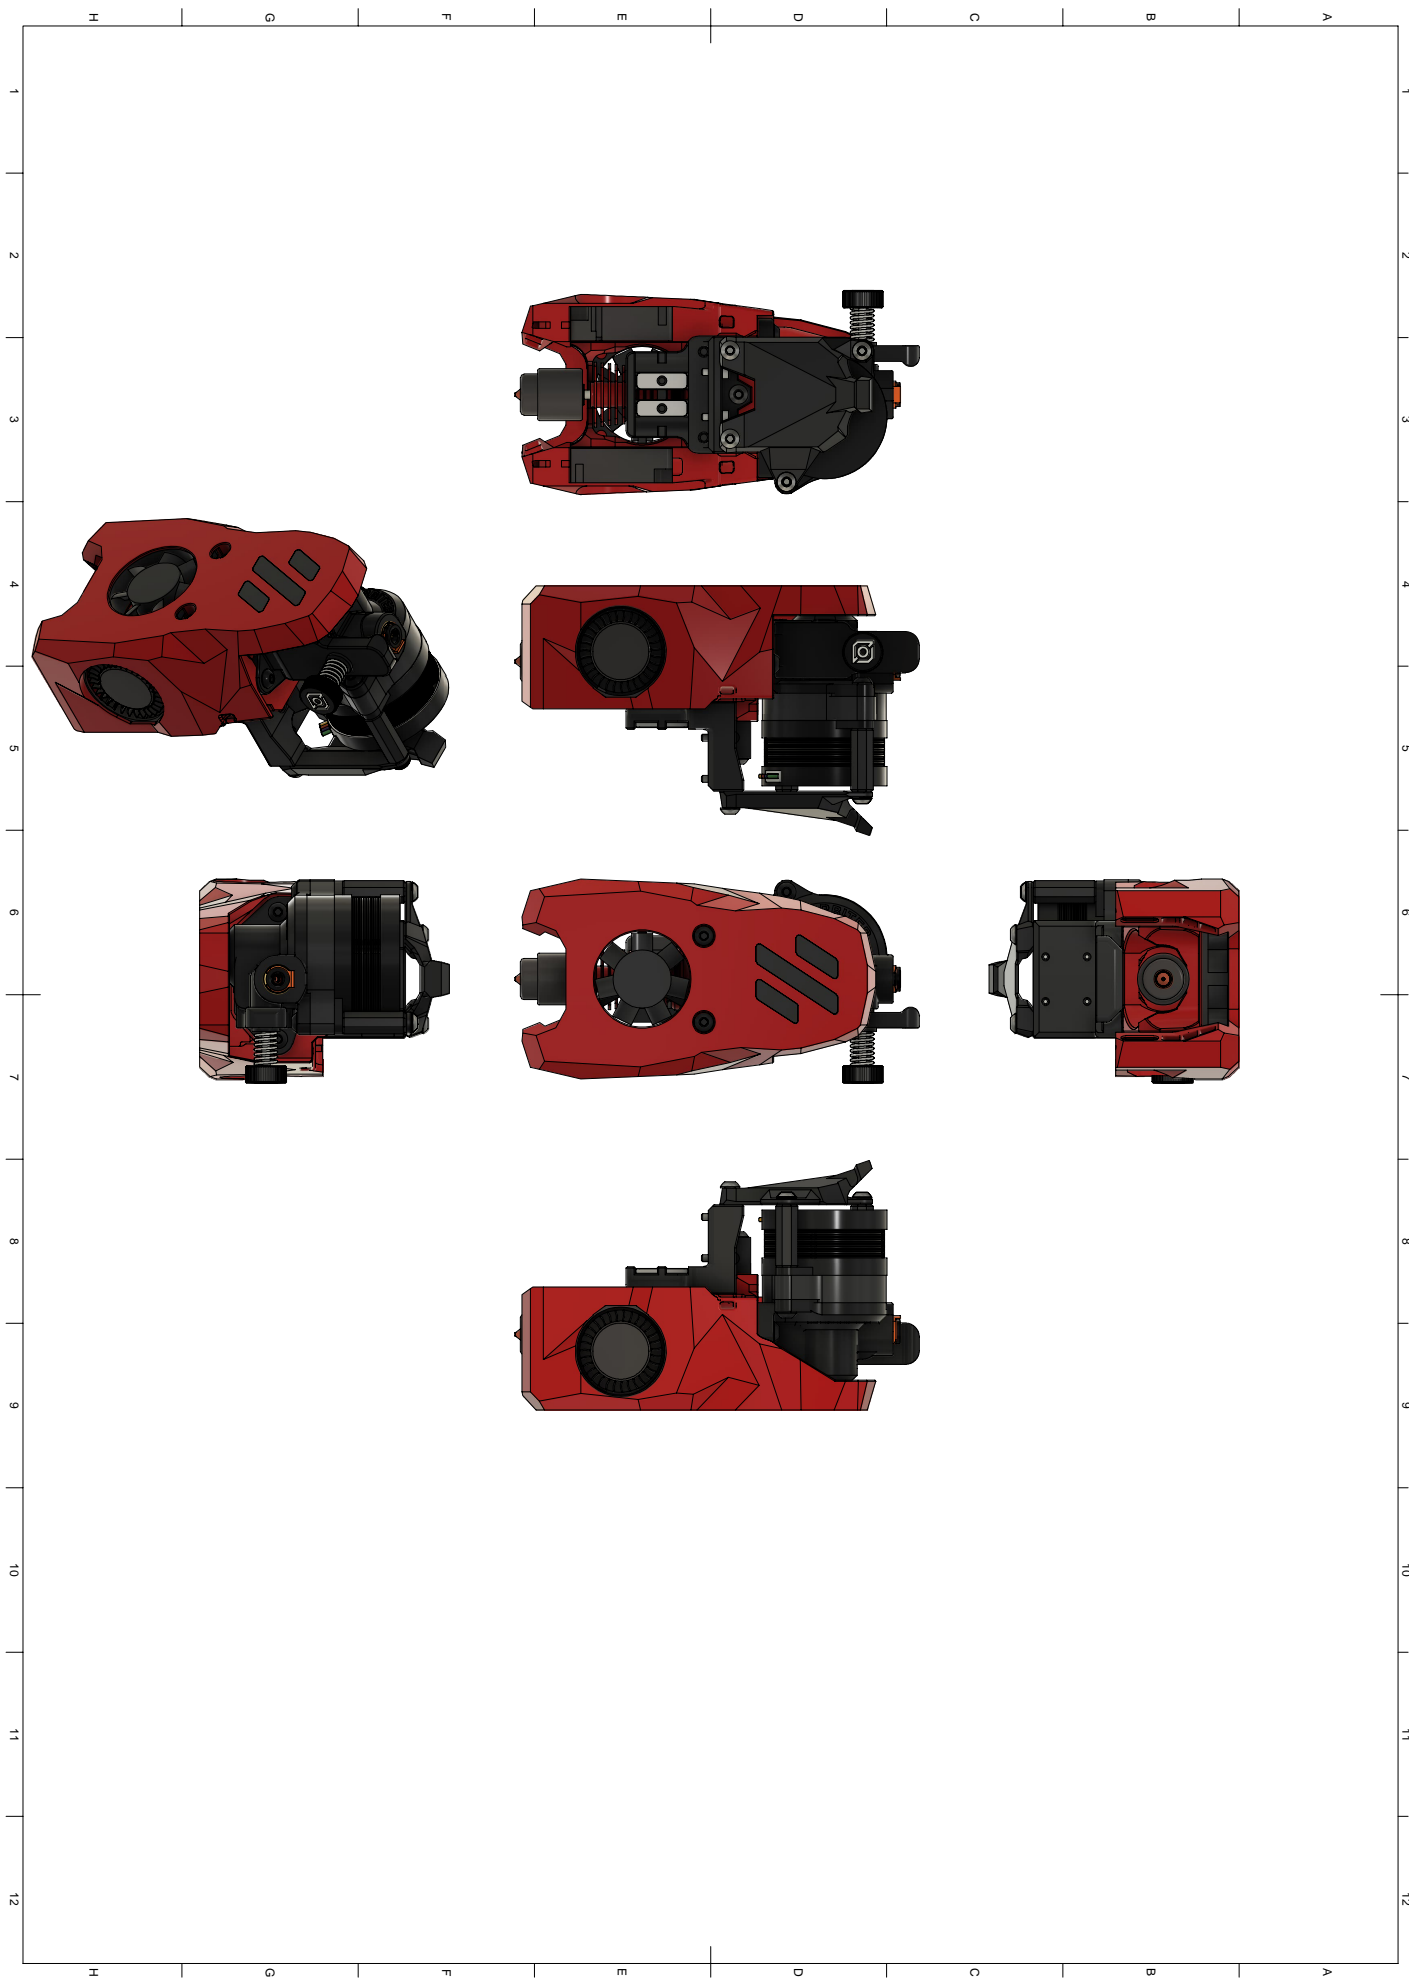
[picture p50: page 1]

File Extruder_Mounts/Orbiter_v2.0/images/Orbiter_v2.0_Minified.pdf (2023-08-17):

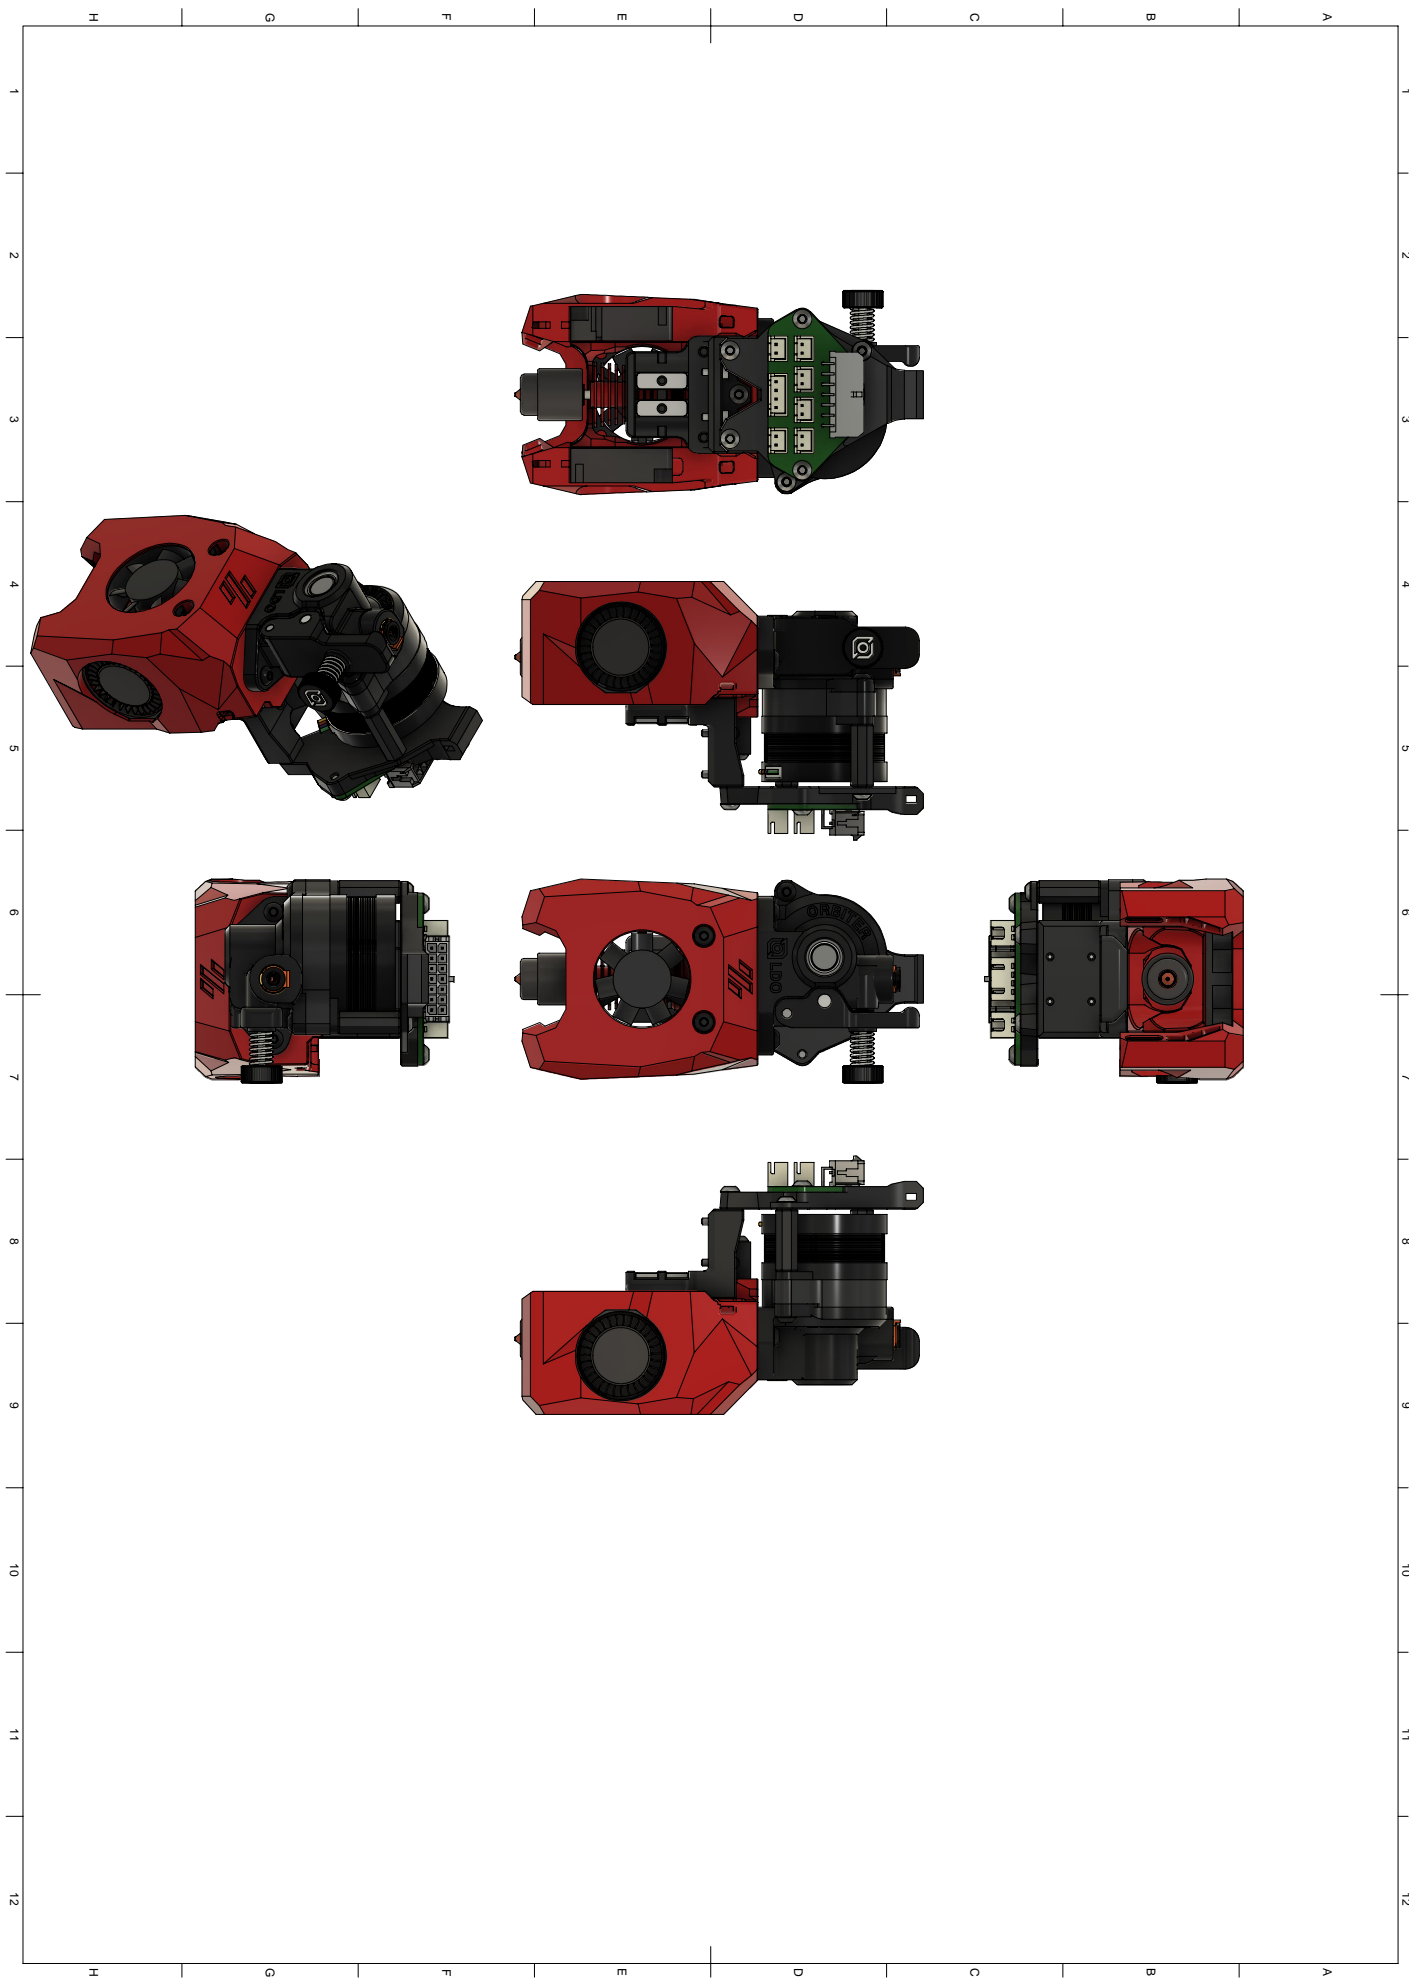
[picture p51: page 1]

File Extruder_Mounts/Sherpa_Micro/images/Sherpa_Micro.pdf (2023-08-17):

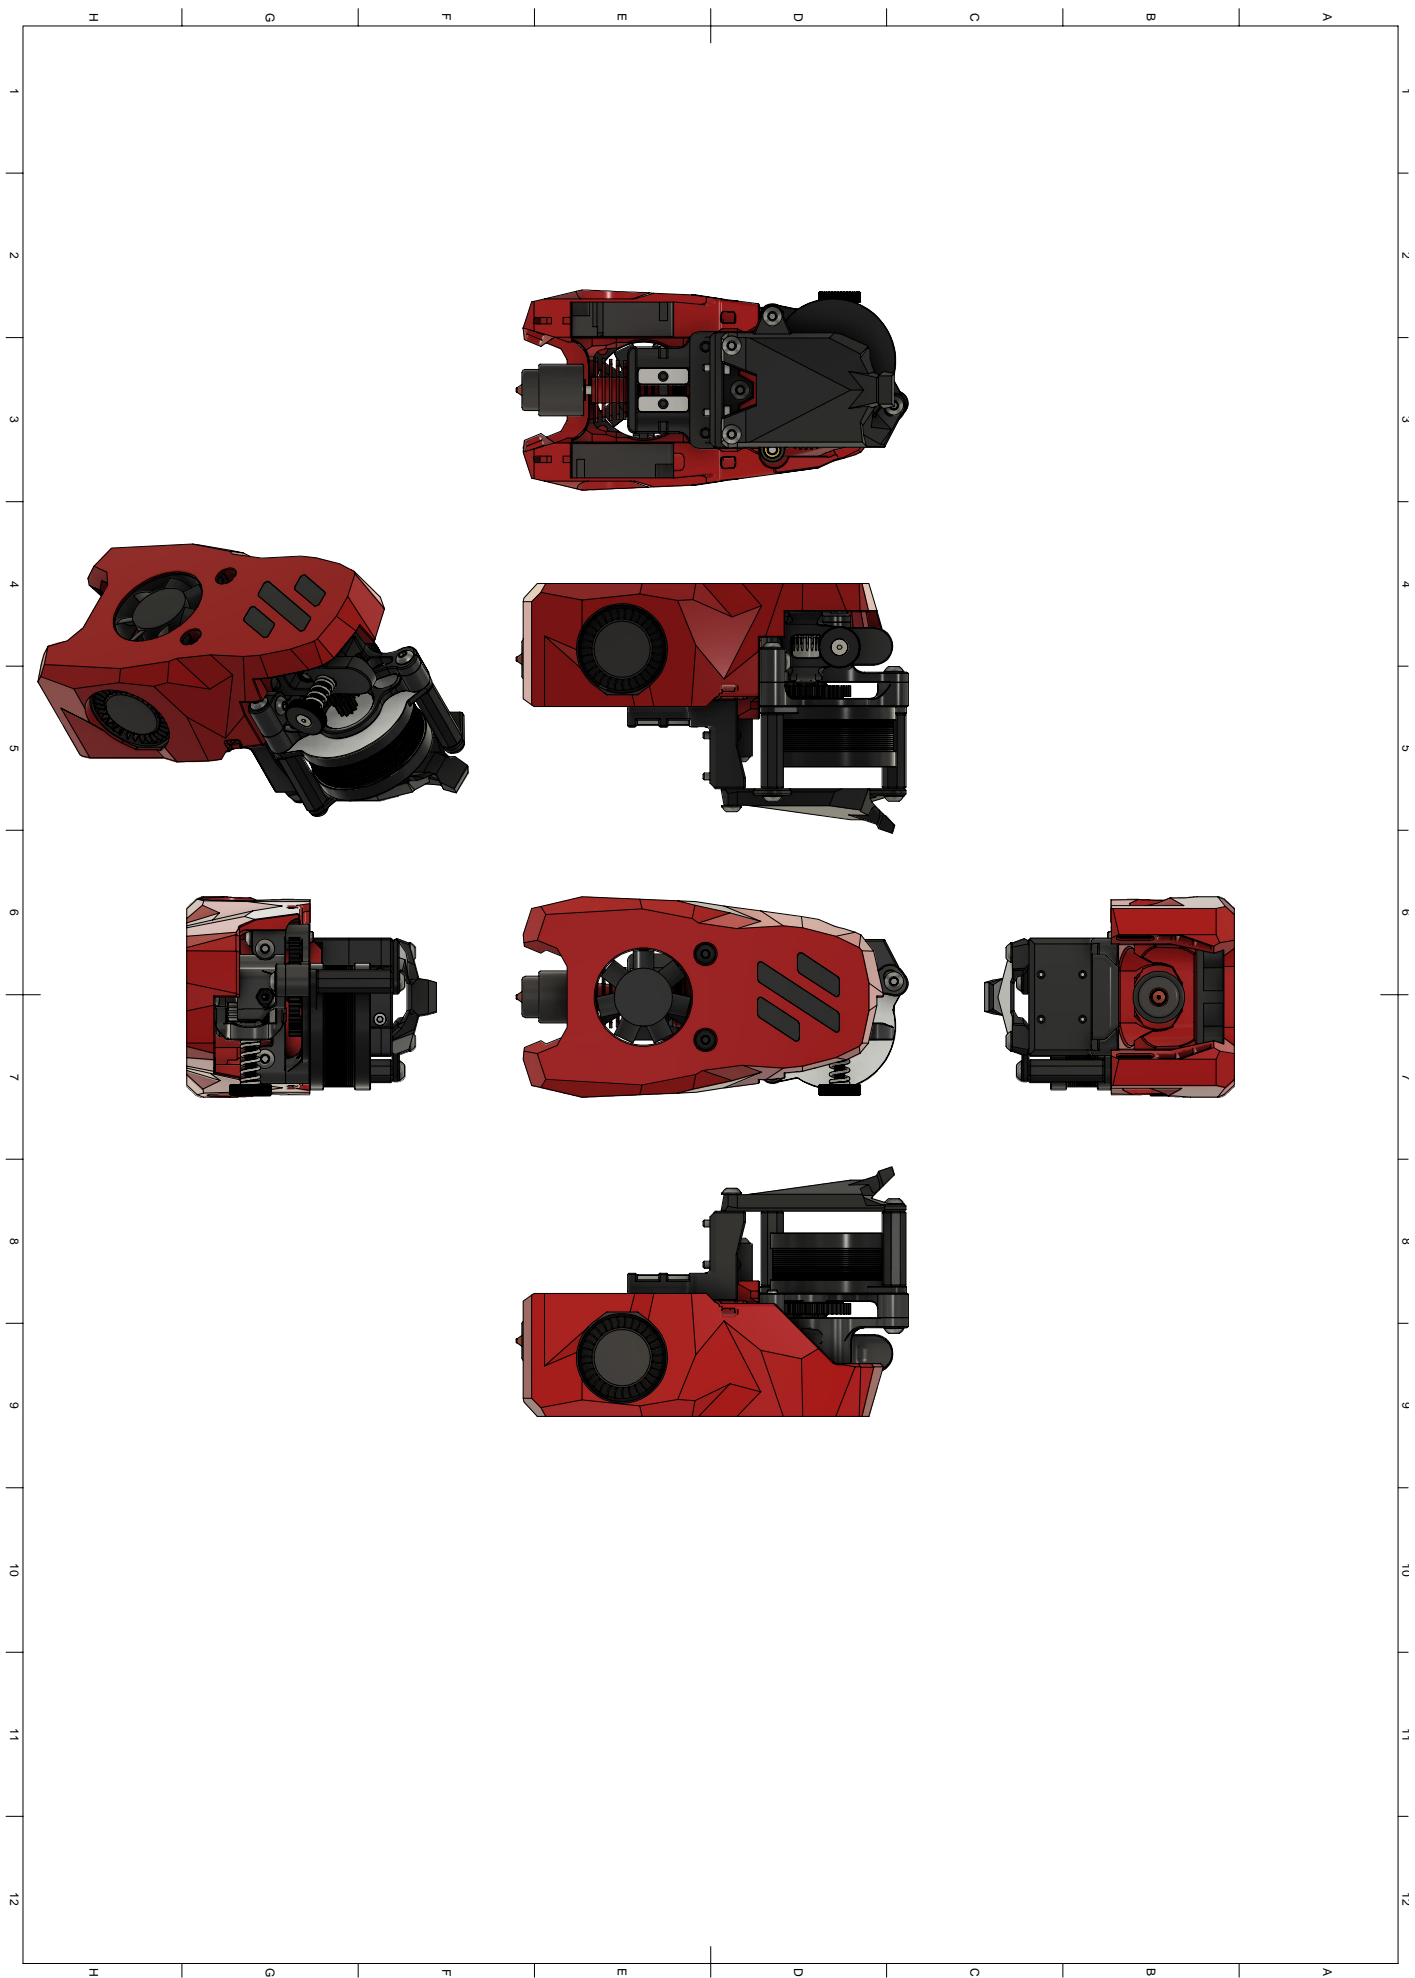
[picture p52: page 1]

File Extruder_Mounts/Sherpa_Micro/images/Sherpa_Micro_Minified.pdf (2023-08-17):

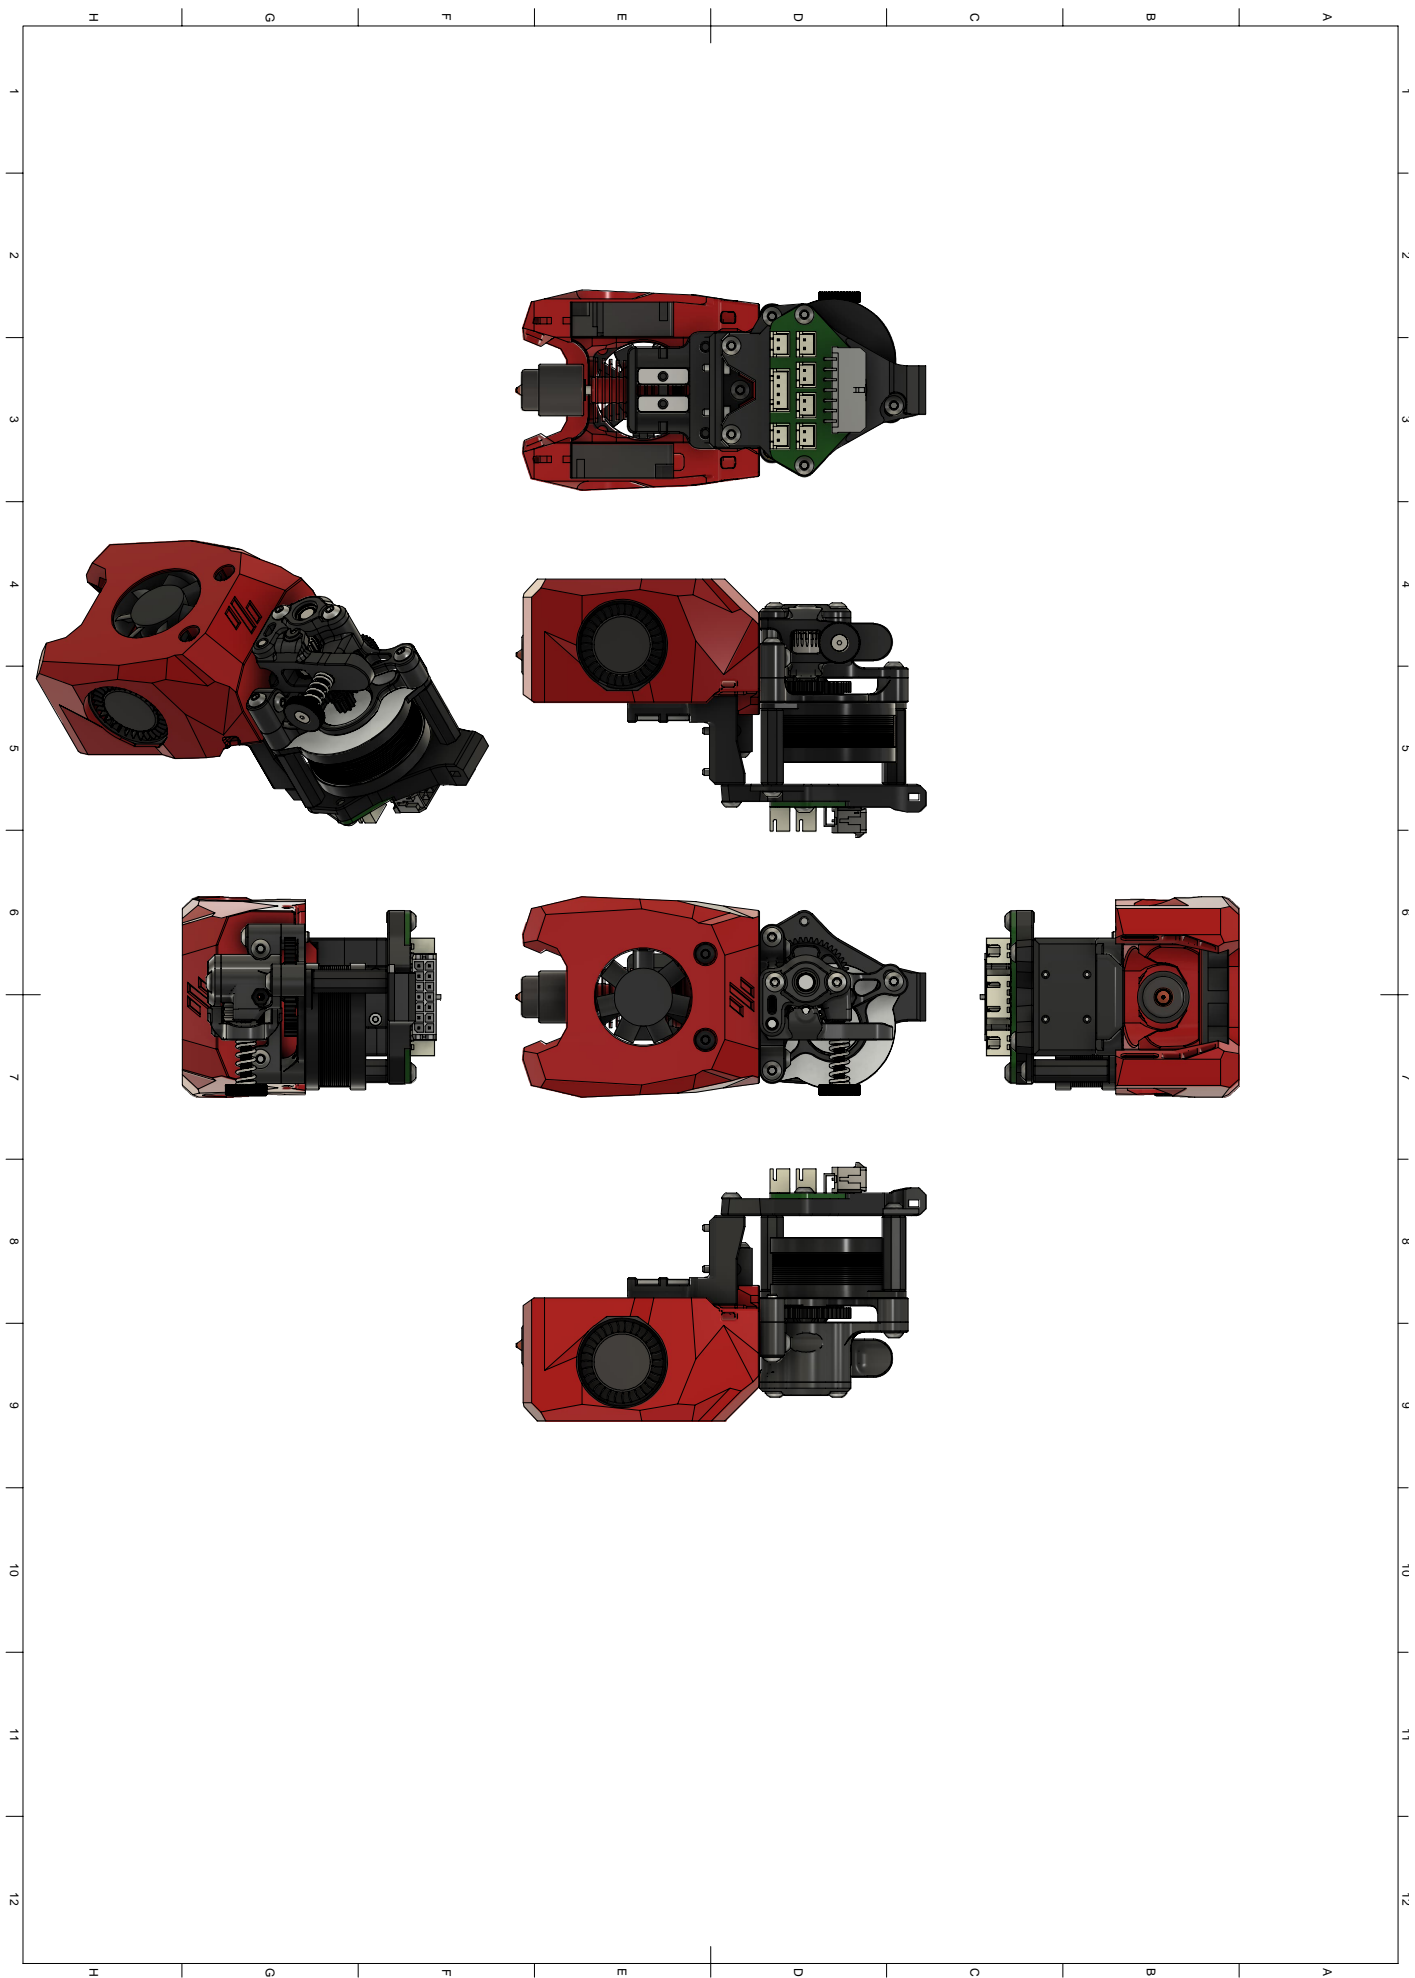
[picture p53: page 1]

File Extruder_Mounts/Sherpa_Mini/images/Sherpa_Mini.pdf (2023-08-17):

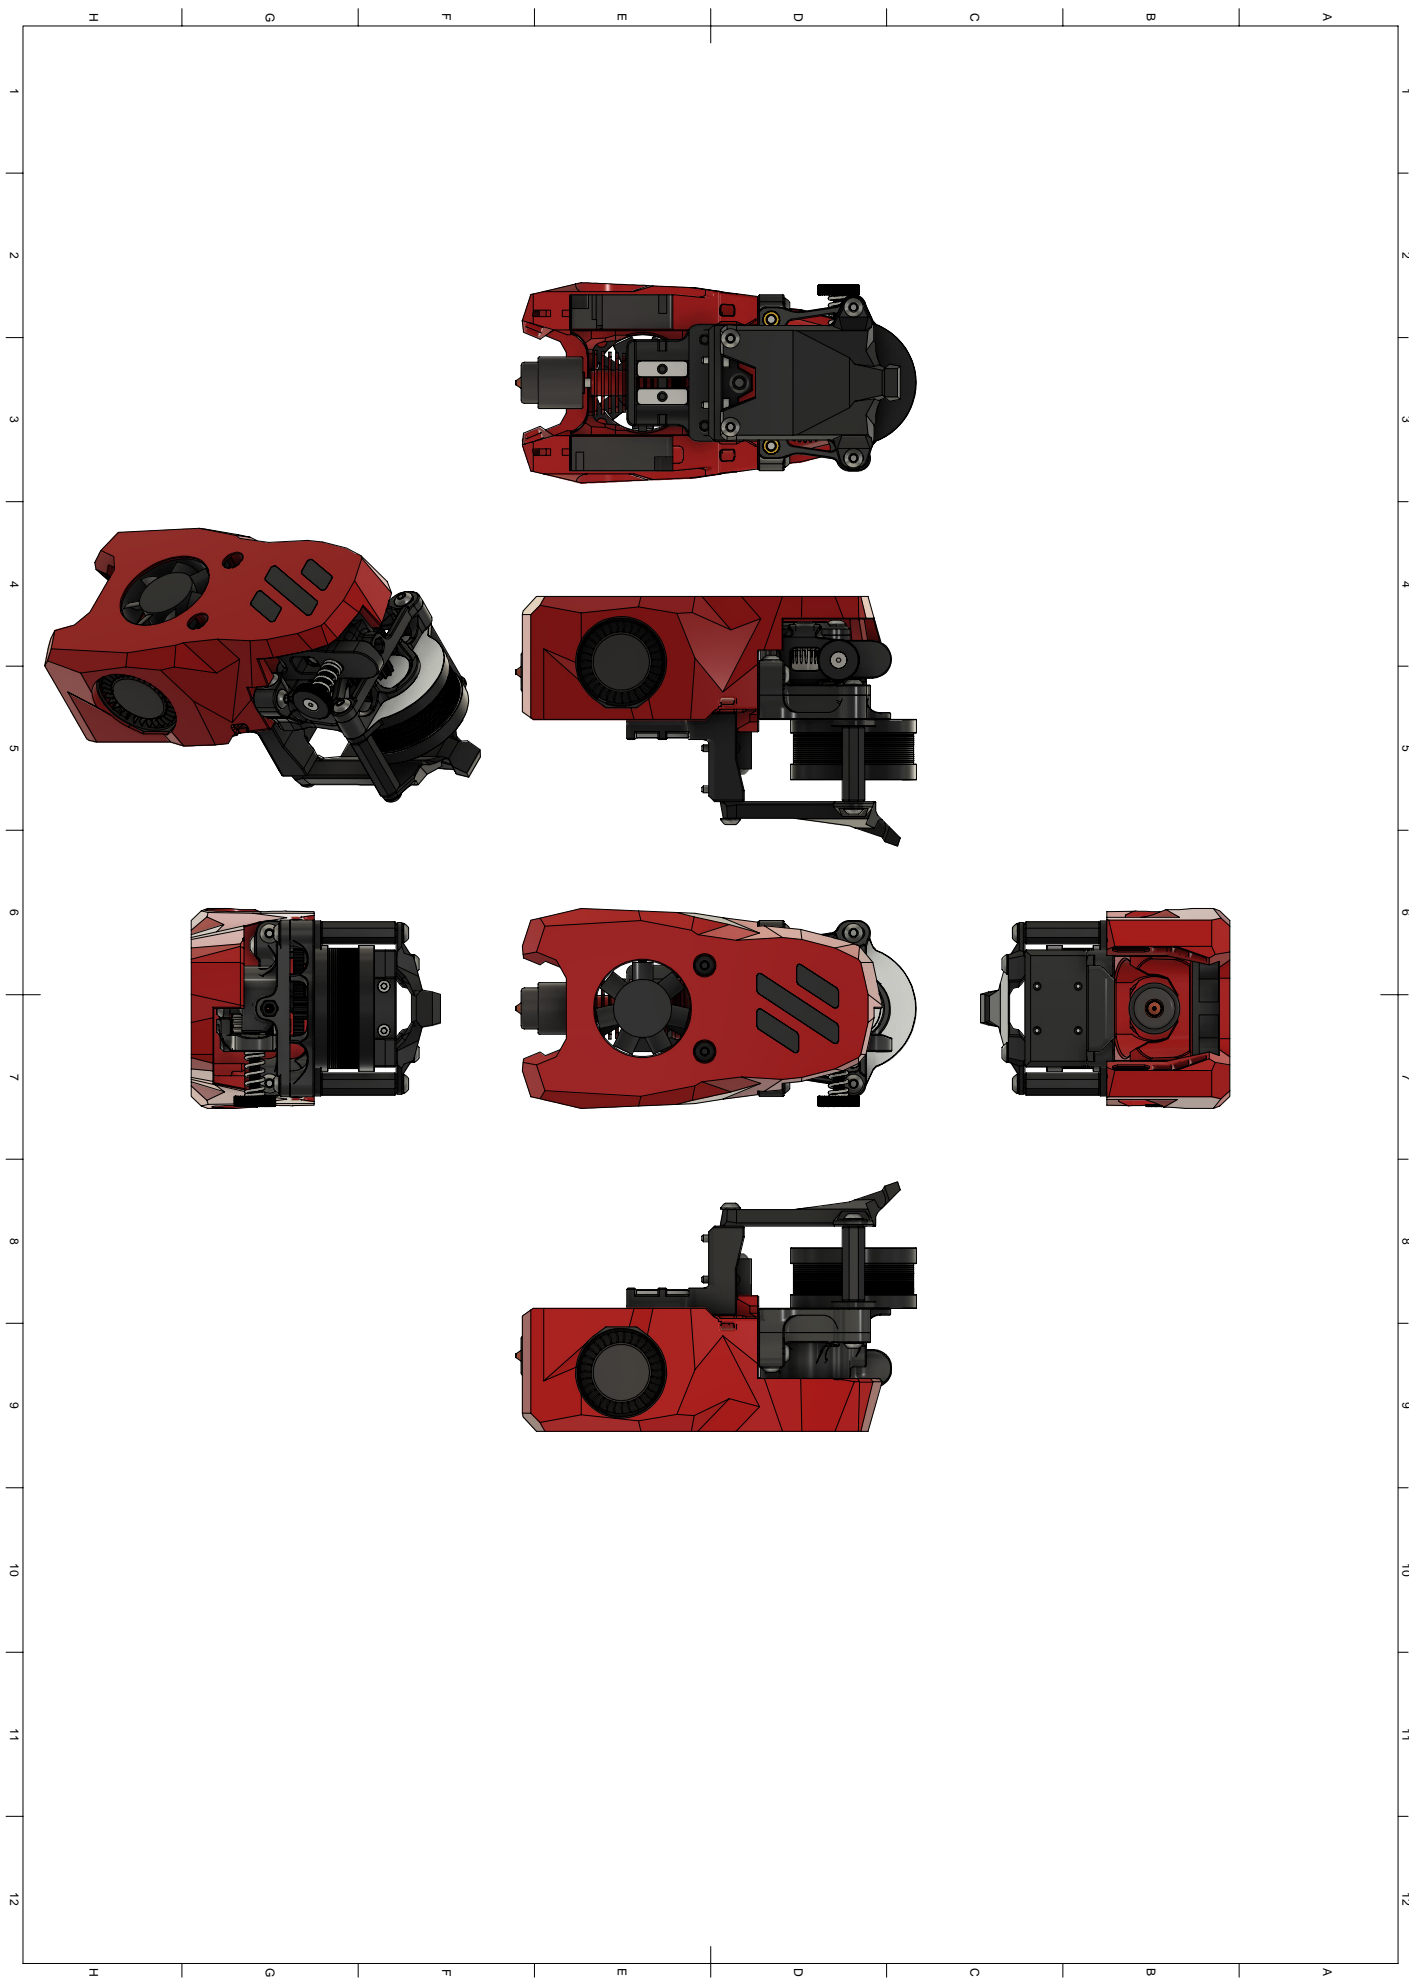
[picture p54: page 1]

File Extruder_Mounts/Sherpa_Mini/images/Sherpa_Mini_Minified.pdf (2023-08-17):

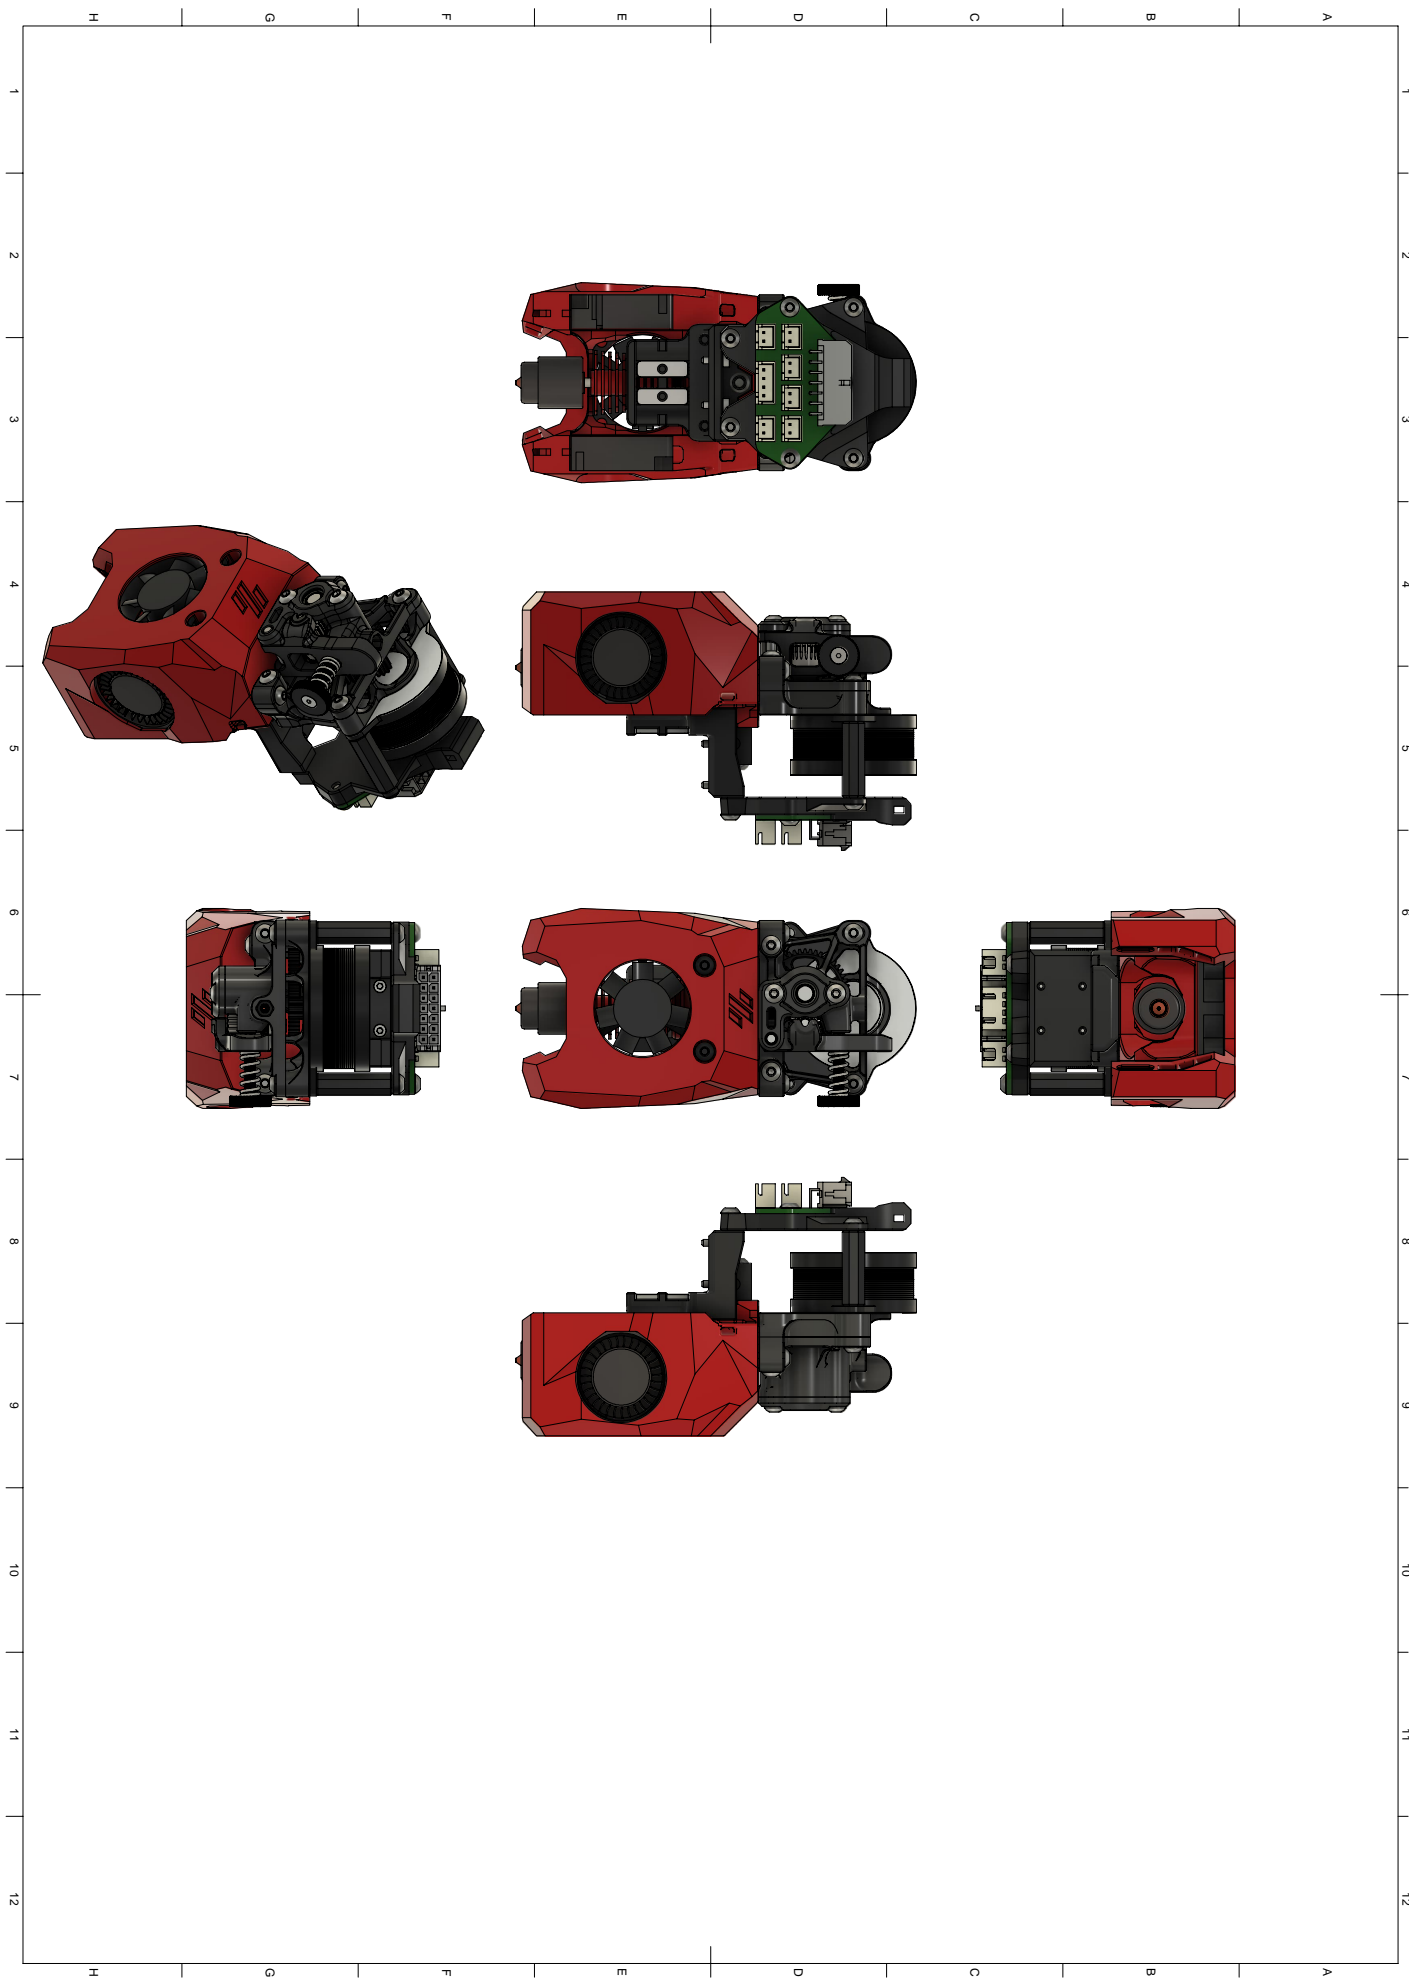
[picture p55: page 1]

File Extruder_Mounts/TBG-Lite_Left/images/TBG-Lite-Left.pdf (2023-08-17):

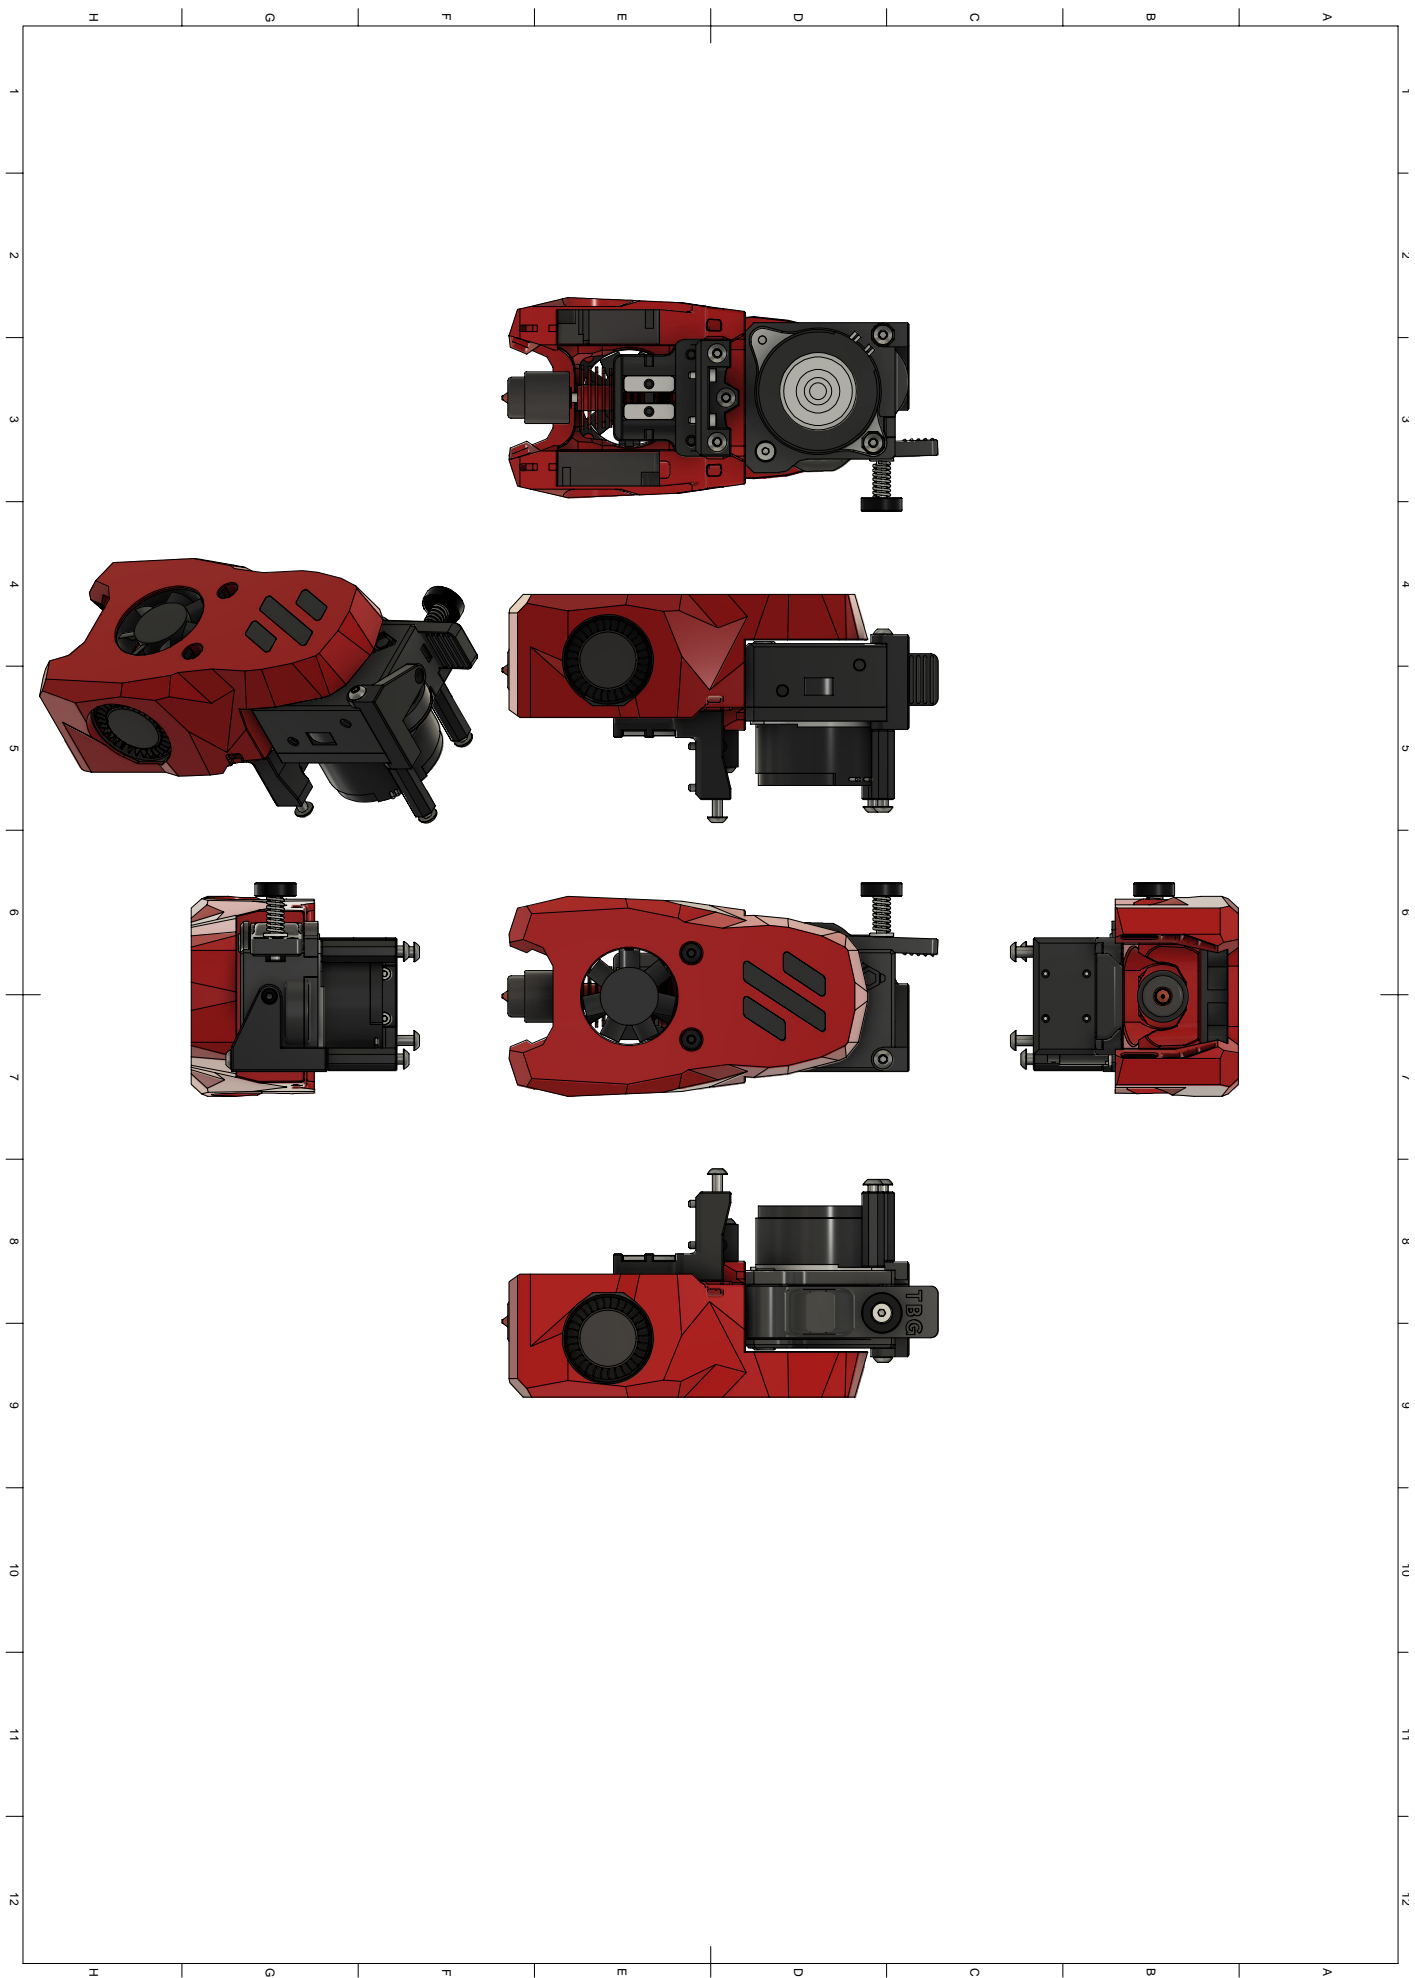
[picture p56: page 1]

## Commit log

2023-02-24 Move Spacer Folder
    [Octagon Spacer v1.step, Octagon_Spacer_17.35mm.stl, Octagon_Spacer_17.60mm.stl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]
2023-02-24 Visual Updates to CAD and images
    - Updated TBG-Lite Left and Libra Mini CAD. Exported new images.
    - Added Shifted Version of sidebar background images
2023-02-25 Clarify Vz-Hextrudort Version
    [MiniSB Umbilical VzHexztrudort Low v5.step, Strain_Relief_Plate_Alternative_x1.stl, Strain_Relief_Plate_x1.stl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]
2023-02-28 Update VzHextrudort, add Orbiter v1.5 and Apus Extruder
    - visual updates to Vz-Hextrudort CNC Low
    - Added experimental Versions of Orbiter v1.5 and Apus-Extruder
    [Apus_Adapter_x1.stl, BOM.ods, MiniSB Umbilical Orbiter v1.5 v5.step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]
2023-03-01 Update TBG-Lite PTFE Holder
    [PTFE_Holder_mirrored_x1.stl, PTFE_Holder_x1.stl]
2023-03-01 Update Umbilical Plate to increase Ziptie-slot strength
    [MiniSB Umbilical Libra Mini v3.step, MiniSB Umbilical Libra Mini v4.step, MiniSB Umbilical Orbiter v1.5 v5.step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]
2023-03-01 Umbilical PCB Updates
    - Updated umbilical Plate to give the Microfit Plug more space to be plugged
    - Added Apus Umbilical Plate
    - Removed outdated CAD-Files
    - added missing chamfer on Apus strain-relief
    [MiniSB Umbilical Apus v3.step, MiniSB Umbilical Libra Mini v4.step, MiniSB Umbilical Libra Mini v5.step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]
2023-03-06 Clarify BOM, add some Assembly Notes
2023-03-06 Add note on PTFE-Lengths, Update Apus-Adapter
    [Apus_Adapter_x1.stl]
2023-03-07 Add missing Hex-Nut to BOM and instructions
2023-03-07 Improve Apus-Parts printability
    [Apus_Adapter_x1.stl]
2023-03-07 Make Orbiter v1.5 alt. Strain-relief default
    [BottomSpacer_x2.stl, Strain_Relief_Plate_Alternative_x1.stl, Strain_Relief_Plate_x1.stl]
2023-03-11 Big update
    - reduce number of strain-reliefs: dropped "standard" strain relief as these were inferior in pretty much all instances.
    - consolidate CAD-Files, now there is only one Assembly file per Mount
    - Add Assembly Manuals for all Mounts.
    - Moved Apus and Orbiter v1.5 from Experimental, as both fit their cowling and strain-reliefs fine however they have not been tested in an actual printer yet.
    - Reworked BOMs
    - Update Images
    [Apus_Adapter_x1.stl, BottomSpacer_left_x1.stl, BottomSpacer_right_x1.stl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]
2023-03-11 Remove outdated Files
    [BOM.ods, SpacerSizes.ods]
2023-03-15 Spelling fix and file count reduction
    [Strain_Relief_Plate_x1.stl, Umbilical_Plate_x1.stl]
2023-03-16 Add One Fits Most Version
    [Orbiter_v2.0_Adapter_CAD_x1.stl, Orbiter_v2.0_Adapter_Offset_x1.stl, Orbiter_v2.0_Strain_Relief_Plate_x1.stl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]
2023-06-13 Update Cowlings to v0.2r1 ducts
2023-07-29 Rapido/Dragon UHF and OneFitsMost Updates
    [[a]_FS_Phaetus_Dragon_UHF_Hotend_Mount.stl]
2023-08-17 Add LGX-Lite, Small Update to Rear of Cowlings
    [Octagon_Spacer_17.50mm.stl, Octagon_Spacer_18.00mm.stl, Octagon_Spacer_18.50mm.stl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]
2023-08-29 Late August Update
    [Apus_Adapter_x1.stl, BottomSpacer_left_x1.stl, BottomSpacer_right_x1.stl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]
2023-09-22 Rename HF folders
    Hopefully this clears up some possible misunderstandings about what Hotends these are for
2023-11-15 Experimental Boop Support
    Added Boop Support (untested)
    Fixed names of OneFitsMost, Sherpa Micro and TBG-Lite-Left STLs.
    (Re-) Added a small gap to the hexagonal contact between x-carriage and cowling, like in the original Mini-Stealthburner.
    [CAN_Plate_Sherpa-Micro_x1.stl, CAN_Plate_TBG-Lite-Left_x1.stl, Strain_Relief_Plate_Sherpa-Micro_x1.stl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]
2023-12-26 Christmas update
    [FS_Hotend_Mount_Dragon_Ace.stl, FS_Hotend_Mount_Dragon_UHF.stl, FS_Hotend_Mount_Rapido.stl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]
2023-12-26 Add ZeroClick Offset Mount
    [Hotend_Mount_TriangleLab_DragonAce.step, ZeroClick_Dock_Center_Offset.stl, ZeroClick_Mount_Offset.stl]
2023-12-27 Add Fusion360 STL export script
2024-01-18 Fix Orbiter v2.0 link to wrong spacer
2024-02-12 Update Umbilical_Plate_Orbiter-v2.0_x1.stl
    Added recesses for thruhole parts of the LDO Picobilical Toolhead PCB 1.1.
    This will now work with either Timmit's original Umbilical PCB or LDO's Picobilical PCB.
    [Umbilical_Plate_Orbiter-v2.0_x1.stl]
2024-02-17 Big Update
    [Bottom_Plate_Spacer_LGX-Lite_x2.stl, CAN_Plate_Apus_x1.stl, CAN_Plate_Aquarius_x1.stl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]
